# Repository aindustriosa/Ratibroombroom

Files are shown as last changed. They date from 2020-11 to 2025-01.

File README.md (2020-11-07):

# Ratibroombroom

This repository contains de design files for the electronics part of Ratibroombroom, a maze solving robot designed at [A industriosa](https://aindustriosa.org/).

The board includes an STM32F405RGT6 microcontroller and two DRV8835 H-bridge drivers moving two 610 coreless motors for locomotion. The robot will also include a suction fan mounted on top with another 610 coreless motor driven directly with an IRLML6344 mosfet.

In the sensing aspect, the robot includes four SFH4045N IR LEDs paired with four PT12-21B/TR8 IR photodiodes for wall detection and positioning inside the maze. AS5145B magnetic encoders are used to measure motor movement precisely. The robot includes an MPU9250 9 axis IMU.

For HMI, we included two tactile switches, four LEDs and a buzzer. We are also working in an external OLED display that could be mounted in a separate module.

>THIS IS A WORK IN PROGRESS AND WILL BE UPDATED AS WE ADVANCE IN THE DEVELOPMENT

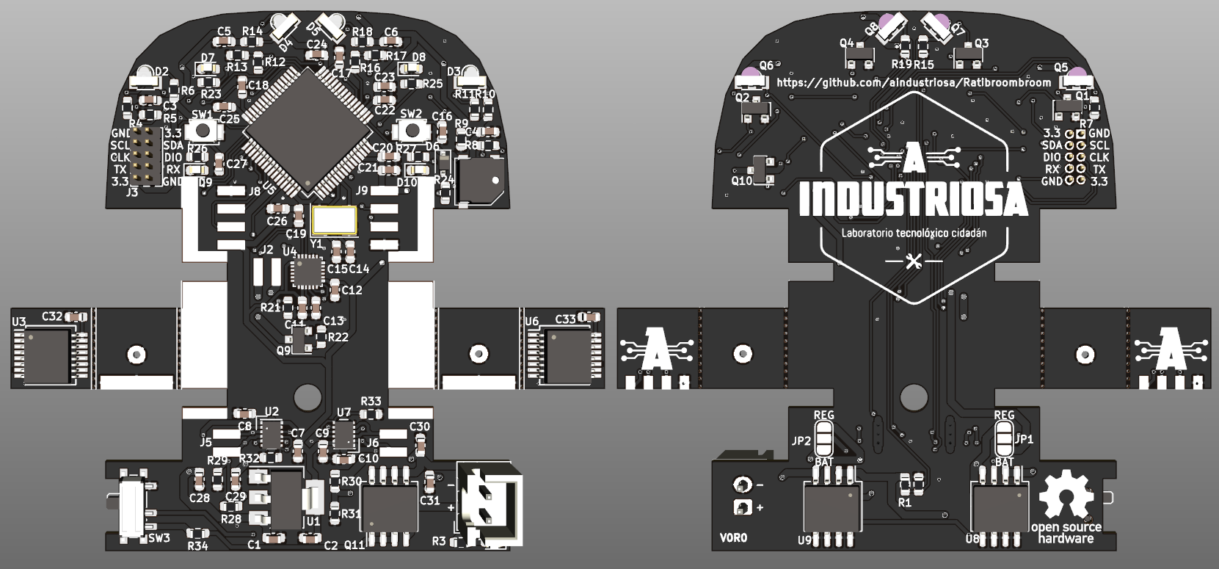
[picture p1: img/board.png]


## Software

The software for this robot will be available in the following repository: [https://github.com/aindustriosa/RatibroombroomSW/](https://github.com/aindustriosa/RatibroombroomSW/)

## Pinout 

Pin # | Function | Peripheral |
----|----|----|
2 | PC13 | Right button (SW2) | 
8 | PC0 | Receiver front right (Q6)  | 
9 | PC1 | Receiver side right (Q8) | 
10 | PC2 | Receiver side left (Q7) | 
11 | PC3 | Receiver front left (Q5) | 
14 | PA0 | LED front left (D7) | 
15 | PA1 | LED front right (D8) | 
16 | PA2 | LED back left (D9)  | 
17 | PA3 | LED back right (D10) | 
20 | PA4 | Emitter front right (D3) | 
21 | PA5 | Emitter side right (D5) | 
22 | PA6 | Emitter side left (D4) | 
23 | PA7 | Emitter front left (D2) | 
24 | PC4 | Battery voltage measurement | 
29 | PB10 | I2C SCL (J3) | 
30 | PB11 | I2C SDA (J3) | 
33 | PB12 | Left button (SW1) |  
35 | PB14 | IMU FSYNC (U4) | 
36 | PB15 | IMU INT (U4) | 
37 | PC6 | Right motor direction (U7) | 
38 | PC7 | Right motor PWM (U7) | 
39 | PC8 | Left motor direction (U2) | 
40 | PC9 | Left motor PWM (U2) | 
42 | PA9 | Serial RX (J3) | 
43 | PA10 | Serial TX (J3) | 
46 | PA13 | SWDIO (J3) | 
49 | PA14 | SWCLK (J3) | 
50 | PA15 | IMU CS (U4) | 
51 | PC10 | IMU SCK (U4) | 
52 | PC11 | IMU MISO (U4) | 
53 | PC12 | IMU MOSI (U4) | 
56 | PB4 | Encoder left, channel A | 
57 | PB5 | Encoder left, channel B | 
58 | PB6 | Encoder right, channel B | 
59 | PB7 | Encoder right, channel A | 
61 | PB8 | Suction fan PWM | 
62 | PB9 | Buzzer (BZ1) | 

## References

This project is heavily based on the work of [cua-cua](https://github.com/cua-cua) and [peque](https://github.com/peque) from [Bulebots](https://github.com/Bulebots) in their projects [Bulebule](https://github.com/Bulebots/bulebule) and [Meiga](https://github.com/Bulebots/meiga)

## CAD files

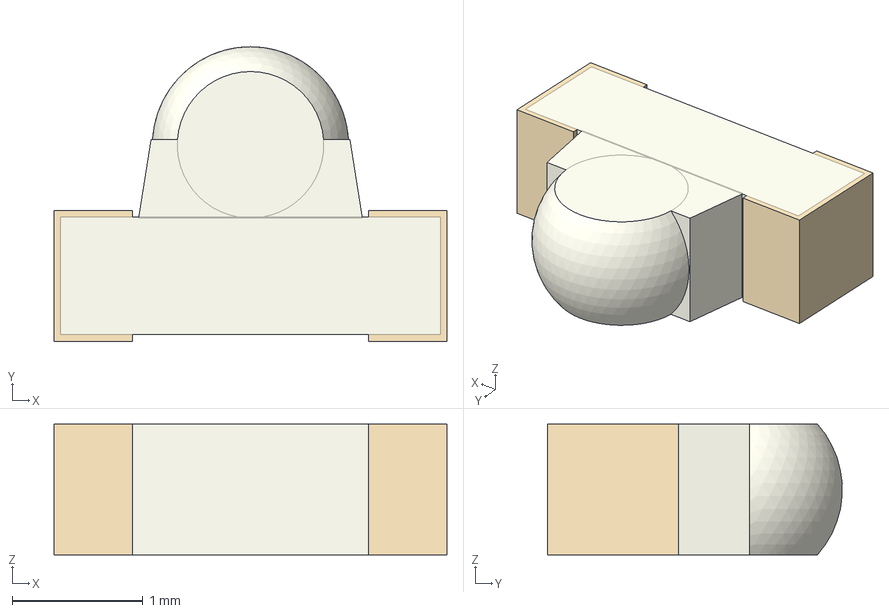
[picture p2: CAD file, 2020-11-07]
3d_models/SFH4045N.step
3.00 x 2.25 x 1.00 mm

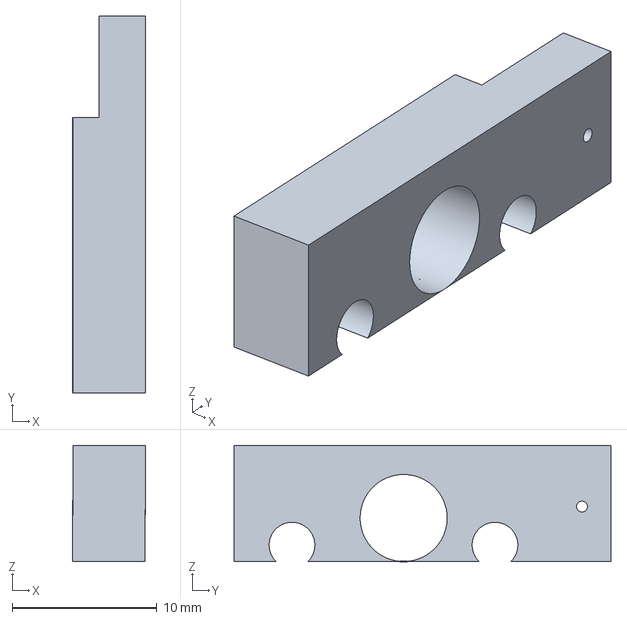
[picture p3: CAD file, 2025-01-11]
cad_design/Ratibroombroom_3d_design_motor_holder-motor_holder_cnc_tolerances.3mf
5.00 x 26.0 x 8.00 mm

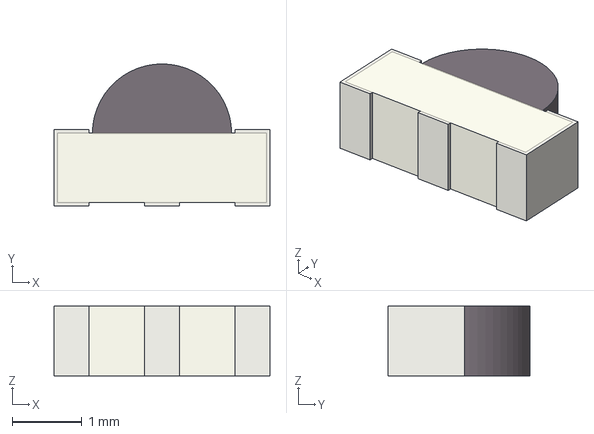
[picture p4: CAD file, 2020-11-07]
3d_models/PT12-21BTR8.step
3.10 x 2.04 x 1.00 mm

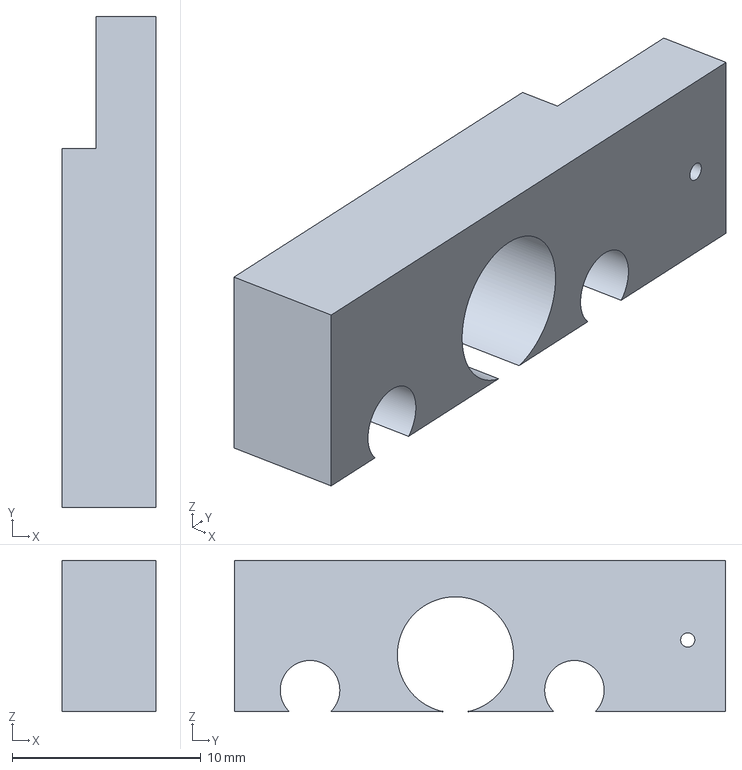
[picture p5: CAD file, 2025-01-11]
cad_design/Ratibroombroom_3d_design_motor_holder-motor_holder_3d_tolerances.3mf
5.00 x 26.0 x 8.00 mm

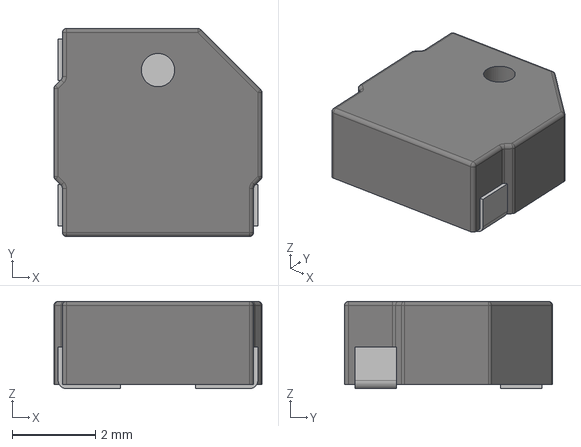
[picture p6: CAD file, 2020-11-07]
3d_models/MLT_5020.step
5.00 x 5.00 x 2.10 mm

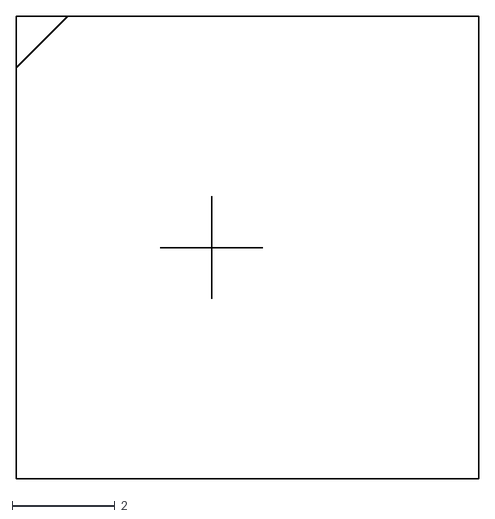
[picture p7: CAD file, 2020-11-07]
cad_design/Encoder_support_Eco1.User.dxf
9.00 x 9.00

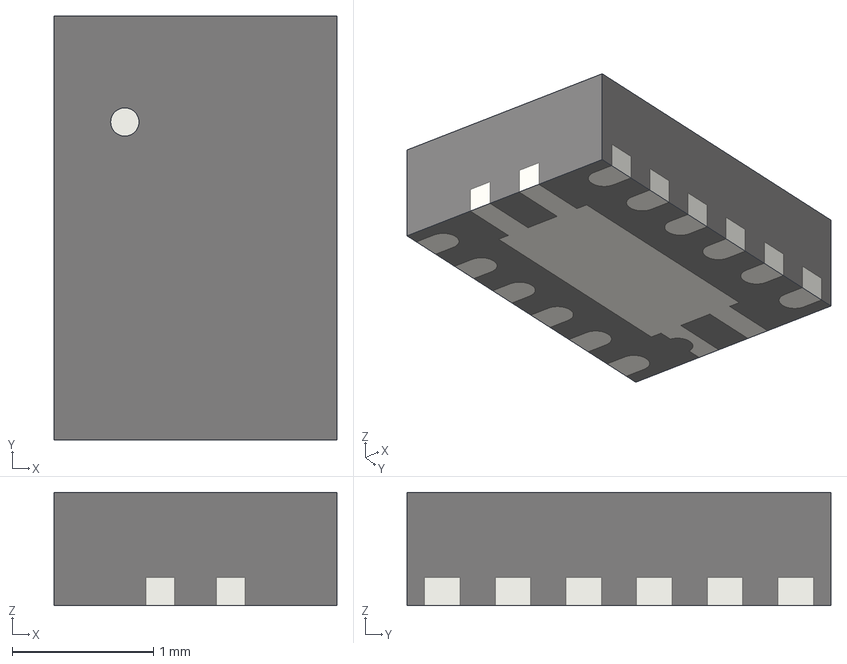
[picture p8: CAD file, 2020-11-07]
3d_models/WSON_12_1EP_3x2mm_P0_5mm_EP1x2_65.step
2.00 x 3.00 x 0.8 mm

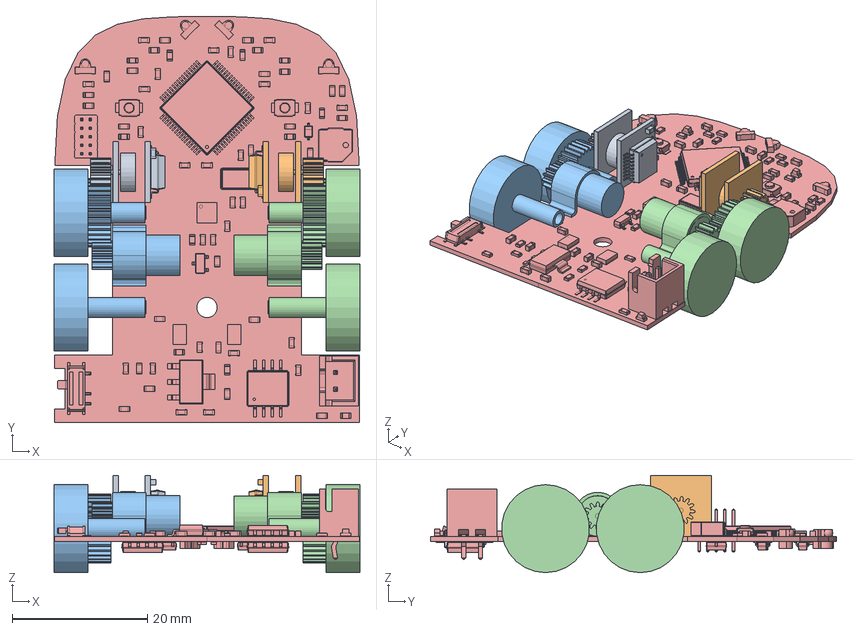
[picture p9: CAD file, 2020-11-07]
cad_design/Ratibroombroom_3d_design.FCStd
45.2 x 60.0 x 14.4 mm
Left encoder
Right encoder
Left drive
Right drive
Board

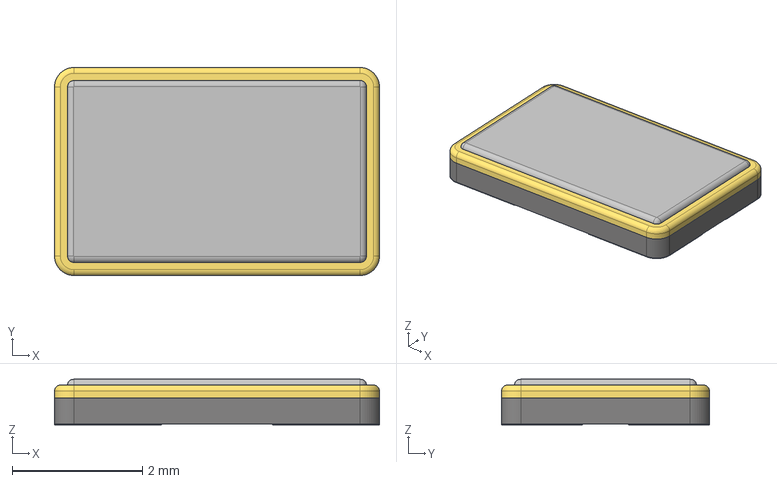
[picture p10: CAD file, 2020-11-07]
3d_models/Crystal_Crystal_SMD_5032_4Pin_5_0x3_2mm.step
5.00 x 3.20 x 0.7 mm

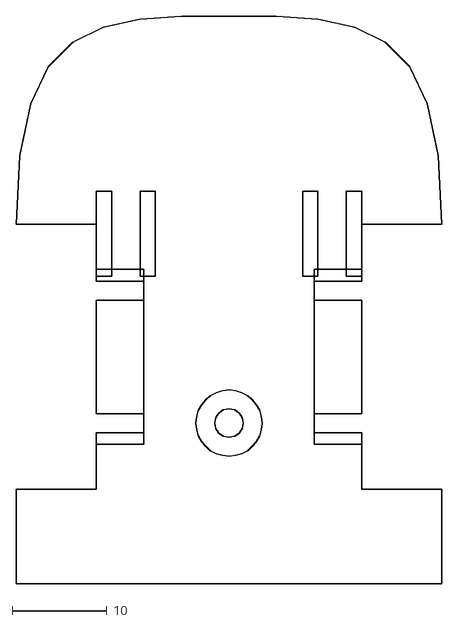
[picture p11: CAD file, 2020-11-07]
cad_design/Board_Eco1.User.dxf
45.0 x 60.0

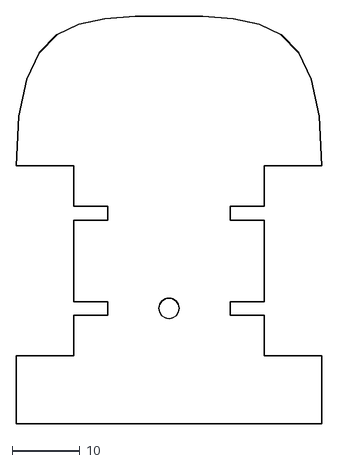
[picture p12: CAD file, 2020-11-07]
cad_design/Board_Edge.Cuts.dxf
45.0 x 60.0

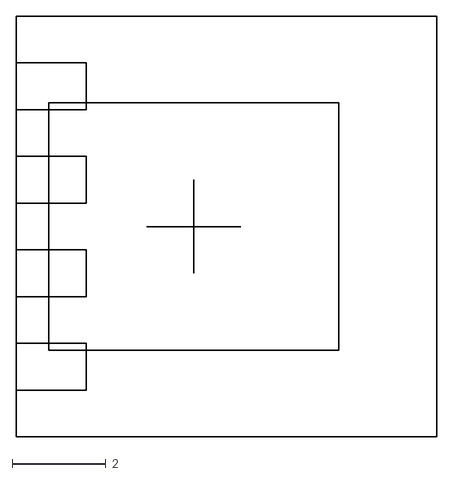
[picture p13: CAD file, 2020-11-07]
cad_design/Encoder_Eco1.User.dxf
9.00 x 9.00

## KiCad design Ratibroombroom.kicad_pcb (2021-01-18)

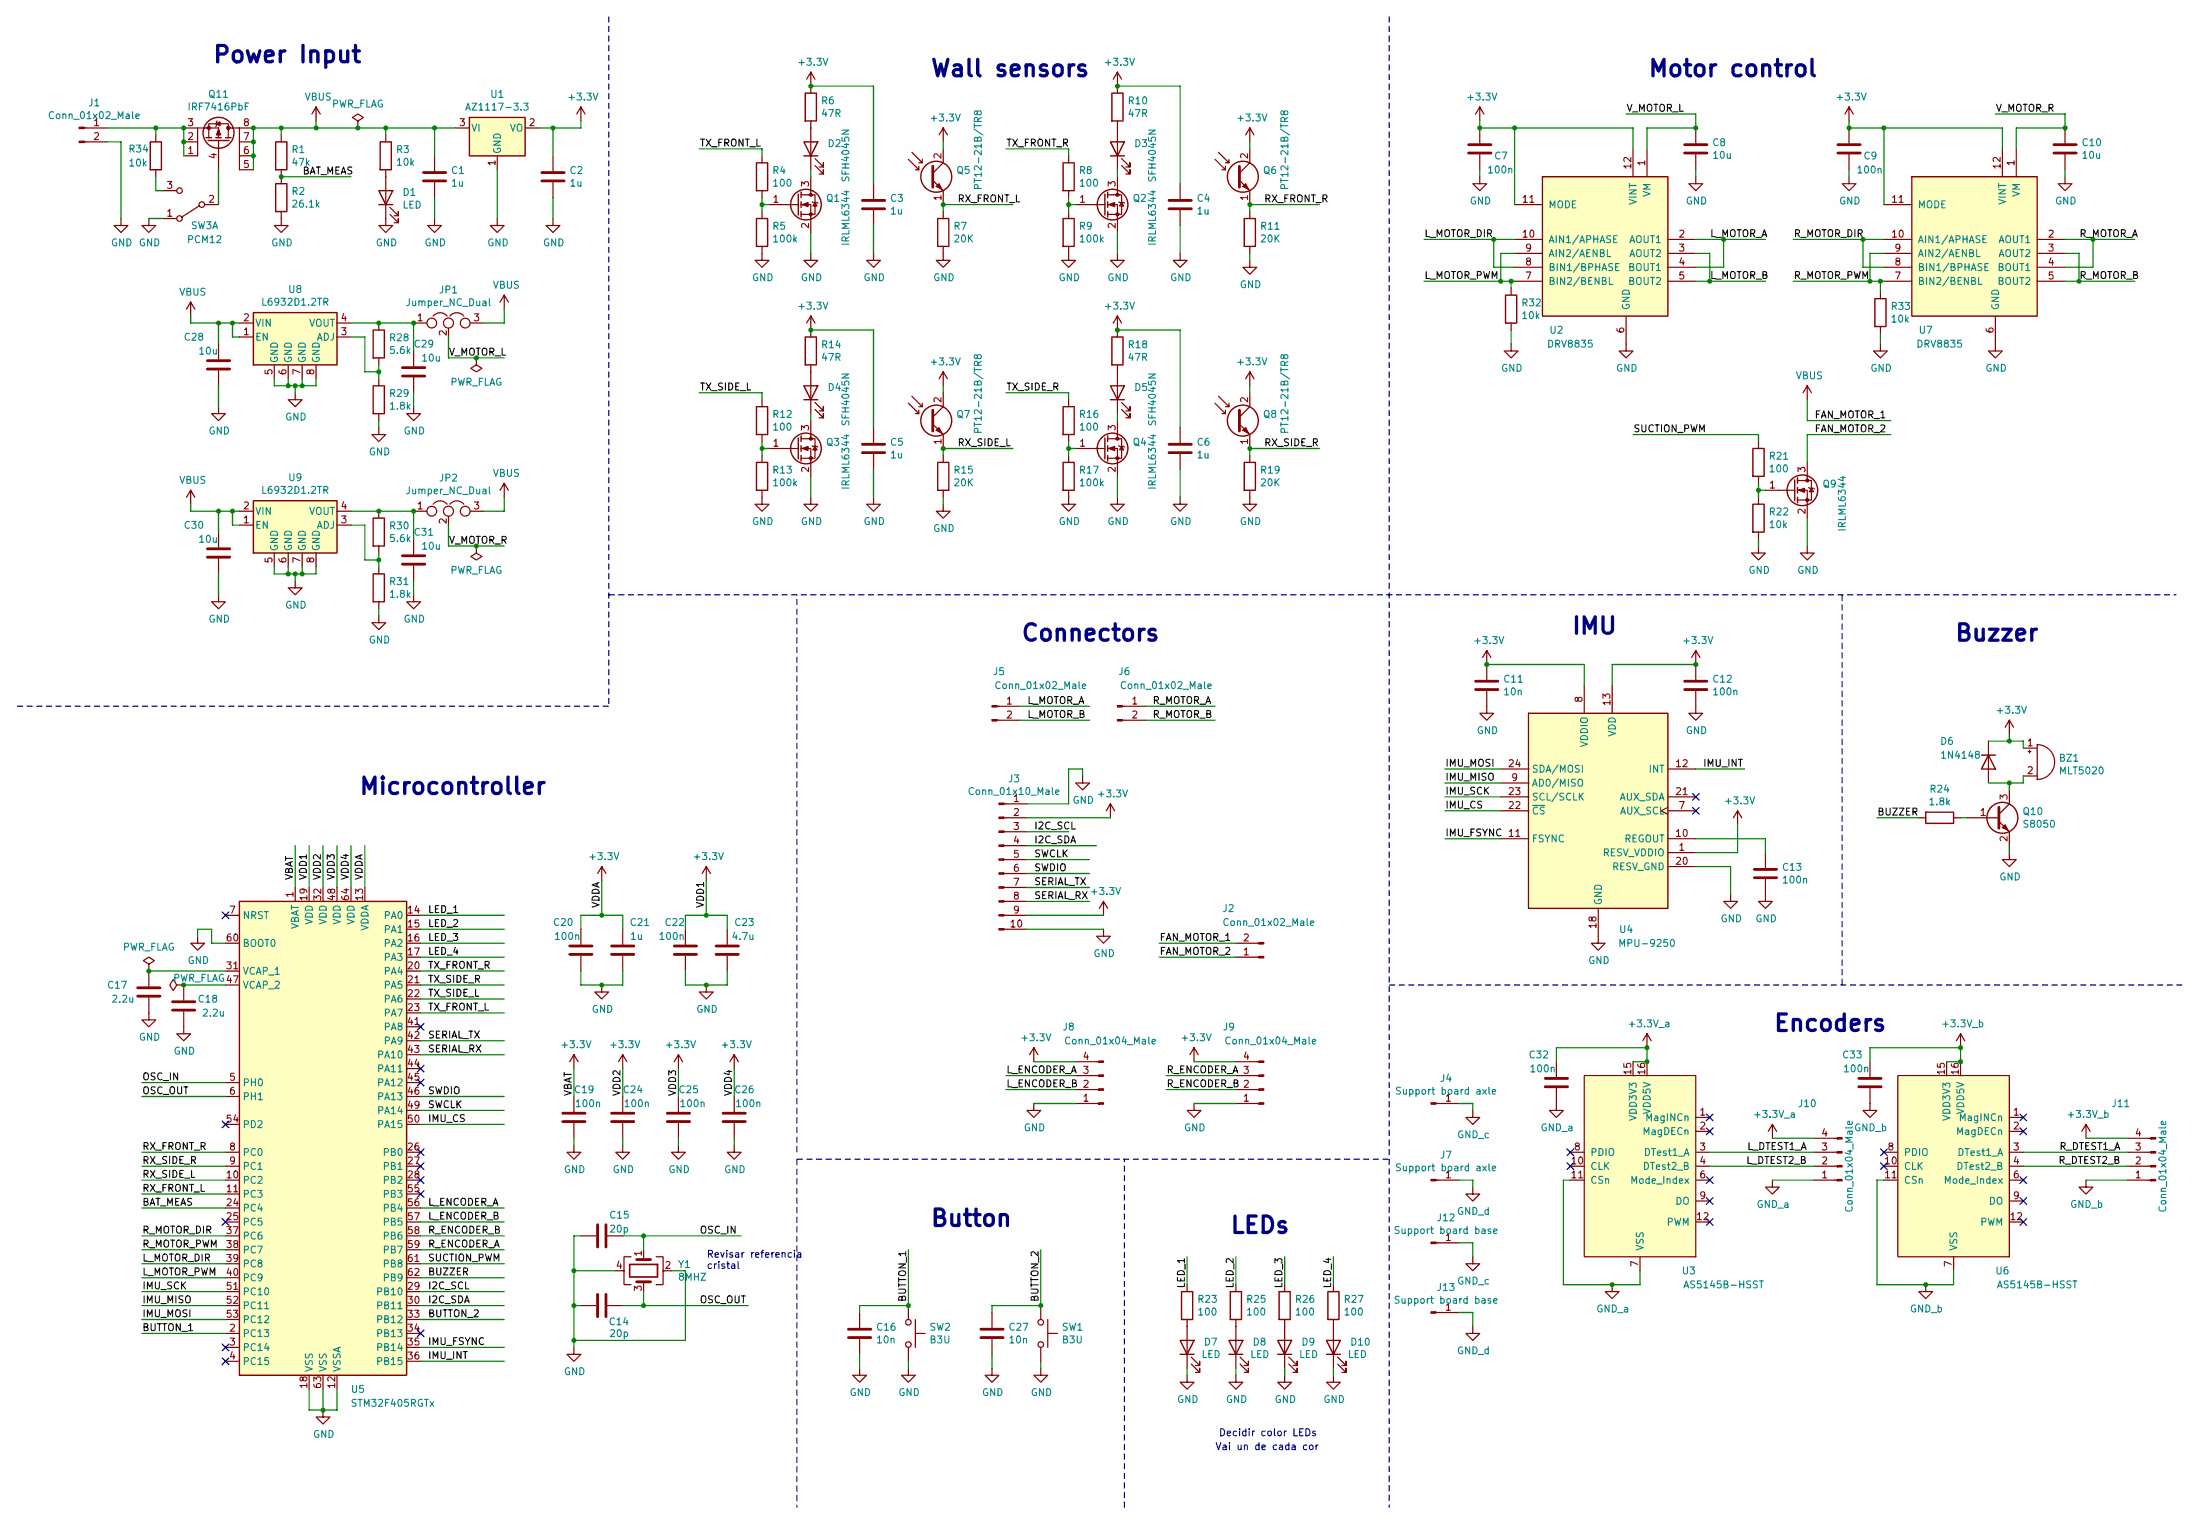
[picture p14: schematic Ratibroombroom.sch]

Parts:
BZ1: MLT5020; MLT-5020
C1, C2, C3, C4, C5, C6, C21: 1u; C_0603_1608Metric
C7, C9, C12, C13, C19, C20, C22, C24, C25, C26, C32, C33: 100n; C_0603_1608Metric
C8, C10, C28, C29, C30, C31: 10u; C_0603_1608Metric
C11, C16, C27: 10n; C_0603_1608Metric
C14, C15: 20p; C_0603_1608Metric
C17, C18: 2.2u; C_0603_1608Metric
C23: 4.7u; C_0603_1608Metric
D1, D7, D8, D9, D10: LED; LED_0603_1608Metric
D2, D3, D4, D5: SFH4045N
D6: 1N4148; D_SOD-323
J1: Conn_01x02_Male; JST_XH_B2B-XH-A_1x02_P2.50mm_Vertical
J2, J5, J6: Conn_01x02_Male; Pad_SMD_2P_1x3mm
J3: Conn_01x10_Male; PinHeader_2x05_P1.27mm_Vertical
J4, J7: Support board axle; Encoder_axle_hole
J8, J9: Conn_01x04_Male; Pad_SMD_4P_1x3mm
J10, J11: Conn_01x04_Male; Pad_SMD_4P_1x1.5mm
J12, J13: Support board base; Encoder_base_connector
JP1, JP2: Jumper_NC_Dual; SolderJumper-3_P1.3mm_Open_RoundedPad1.0x1.5mm_NumberLabels
Q1, Q2, Q3, Q4, Q9: IRLML6344; SOT-23
Q5, Q6, Q7, Q8: PT12-21B/TR8; PT12-21B-TR8
Q10: S8050; SOT-23
Q11: IRF7416PbF; SO-8_5.3x6.2mm_P1.27mm
R1: 47k; R_0603_1608Metric
R2: 26.1k; R_0603_1608Metric
R3, R22, R32, R33, R34: 10k; R_0603_1608Metric
R4, R8, R12, R16, R21, R23, R25, R26, R27: 100; R_0603_1608Metric
R5, R9, R13, R17: 100k; R_0603_1608Metric
R6, R10, R14, R18: 47R; R_0603_1608Metric
R7, R11, R15, R19: 20K; R_0603_1608Metric
R24, R29, R31: 1.8k; R_0603_1608Metric
R28, R30: 5.6k; R_0603_1608Metric
SW1, SW2: B3U; SW_SPST_B3U-1000P
SW3: PCM12; SW_SPDT_PCM12
U1: AZ1117-3.3; SOT-223-3_TabPin2
U2, U7: DRV8835; WSON-12-1EP_3x2mm_P0.5mm_EP1x2.65_ThermalVias
U3, U6: AS5145B-HSST; SSOP-16_5.3x6.2mm_P0.65mm
U4: MPU-9250; QFN-24-1EP_3x3mm_P0.4mm_EP1.75x1.6mm
U5: STM32F405RGTx; LQFP-64_10x10mm_P0.5mm
U8, U9: L6932D1.2TR; SO-8_5.3x6.2mm_P1.27mm
Y1: 8MHZ; Crystal_SMD_5032-4Pin_5.0x3.2mm

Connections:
+3.3V_a: C32.2, J10.4, U3.15 (VDD3V3), U3.16 (VDD5V)
+3.3V_b: C33.2, J11.4, U6.15 (VDD3V3), U6.16 (VDD5V)
+3V3: BZ1.1 (-), C2.1, C3.1, C4.1, C5.1, C6.1, C7.1, C9.1, C11.1, C12.1, C19.2, C20.2, C21.2, C22.2, C23.2, C24.2, C25.2, C26.2, D6.1 (K), J3.2, J3.9, J8.4, J9.4, Q5.2 (C), Q6.2 (C), Q7.2 (C), Q8.2 (C), R6.1, R10.1, R14.1, R18.1, U1.2 (VO), U2.11 (MODE), U2.12 (VINT), U4.1 (RESV_VDDIO), U4.8 (VDDIO), U4.13 (VDD), U5.1 (VBAT), U5.13 (VDDA), U5.19 (VDD), U5.32 (VDD), U5.48 (VDD), U5.64 (VDD), U7.11 (MODE), U7.12 (VINT)
/BAT_MEAS: R1.2, R2.1, U5.24 (PC4)
/BUTTON_1: C16.1, SW2.1, U5.2 (PC13)
/BUTTON_2: C27.1, SW1.1, U5.33 (PB12)
/BUZZER: R24.2, U5.62 (PB9)
/FAN_MOTOR_2: J2.1, Q9.3 (D)
/I2C_SCL: J3.3, U5.29 (PB10)
/I2C_SDA: J3.4, U5.30 (PB11)
/IMU_CS: U4.22 (~CS), U5.50 (PA15)
/IMU_FSYNC: U4.11 (FSYNC), U5.35 (PB14)
/IMU_INT: U4.12 (INT), U5.36 (PB15)
/IMU_MISO: U4.9 (AD0/MISO), U5.52 (PC11)
/IMU_MOSI: U4.24 (SDA/MOSI), U5.53 (PC12)
/IMU_SCK: U4.23 (SCL/SCLK), U5.51 (PC10)
/LED_1: R23.1, U5.14 (PA0)
/LED_2: R25.1, U5.15 (PA1)
/LED_3: R26.1, U5.16 (PA2)
/LED_4: R27.1, U5.17 (PA3)
/L_DTEST1_A: J10.3, U3.3 (DTest1_A)
/L_DTEST2_B: J10.2, U3.4 (DTest2_B)
/L_ENCODER_A: J8.3, U5.56 (PB4)
/L_ENCODER_B: J8.2, U5.57 (PB5)
/L_MOTOR_A: J5.1, U2.2 (AOUT1), U2.4 (BOUT1)
/L_MOTOR_B: J5.2, U2.3 (AOUT2), U2.5 (BOUT2)
/L_MOTOR_DIR: U2.8 (BIN1/BPHASE), U2.10 (AIN1/APHASE), U5.39 (PC8)
/L_MOTOR_PWM: R32.1, U2.7 (BIN2/BENBL), U2.9 (AIN2/AENBL), U5.40 (PC9)
/OSC_IN: C15.1, U5.5 (PH0), Y1.1
/OSC_OUT: C14.1, U5.6 (PH1), Y1.3
/RX_FRONT_L: Q5.1 (E), R7.1, U5.11 (PC3)
/RX_FRONT_R: Q6.1 (E), R11.1, U5.8 (PC0)
/RX_SIDE_L: Q7.1 (E), R15.1, U5.10 (PC2)
/RX_SIDE_R: Q8.1 (E), R19.1, U5.9 (PC1)
/R_DTEST1_A: J11.3, U6.3 (DTest1_A)
/R_DTEST2_B: J11.2, U6.4 (DTest2_B)
/R_ENCODER_A: J9.3, U5.59 (PB7)
/R_ENCODER_B: J9.2, U5.58 (PB6)
/R_MOTOR_A: J6.1, U7.2 (AOUT1), U7.4 (BOUT1)
/R_MOTOR_B: J6.2, U7.3 (AOUT2), U7.5 (BOUT2)
/R_MOTOR_DIR: U5.37 (PC6), U7.8 (BIN1/BPHASE), U7.10 (AIN1/APHASE)
/R_MOTOR_PWM: R33.1, U5.38 (PC7), U7.7 (BIN2/BENBL), U7.9 (AIN2/AENBL)
/SERIAL_RX: J3.8, U5.43 (PA10)
/SERIAL_TX: J3.7, U5.42 (PA9)
/SUCTION_PWM: R21.1, U5.61 (PB8)
/SWCLK: J3.5, U5.49 (PA14)
/SWDIO: J3.6, U5.46 (PA13)
/TX_FRONT_L: R4.1, U5.23 (PA7)
/TX_FRONT_R: R8.1, U5.20 (PA4)
/TX_SIDE_L: R12.1, U5.22 (PA6)
/TX_SIDE_R: R16.1, U5.21 (PA5)
/V_MOTOR_L: C8.1, JP1.2, U2.1 (VM)
/V_MOTOR_R: C10.1, JP2.2, U7.1 (VM)
GND: C1.2, C2.2, C3.2, C4.2, C5.2, C6.2, C7.2, C8.2, C9.2, C10.2, C11.2, C12.2, C13.2, C14.2, C15.2, C16.2, C17.1, C18.1, C19.1, C20.1, C21.1, C22.1, C23.1, C24.1, C25.1, C26.1, C27.2, C28.1, C29.1, C30.1, C31.1, D1.1 (K), D7.1 (K), D8.1 (K), D9.1 (K), D10.1 (K), J1.2, J3.1, J3.10, J8.1, J9.1, Q1.2 (S), Q2.2 (S), Q3.2 (S), Q4.2 (S), Q9.2 (S), Q10.2 (E), R2.2, R5.2, R7.2, R9.2, R11.2, R13.2, R15.2, R17.2, R19.2, R22.2, R29.2, R31.2, R32.2, R33.2, SW1.2, SW2.2, SW3.1 (A), U1.1 (GND), U2.6 (GND), U4.18 (GND), U4.20 (RESV_GND), U5.12 (VSSA), U5.18 (VSS), U5.60 (BOOT0), U5.63 (VSS), U7.6 (GND), U8.5 (GND), U8.6 (GND), U8.7 (GND), U8.8 (GND), U9.5 (GND), U9.6 (GND), U9.7 (GND), U9.8 (GND), Y1.2, Y1.4
GND_a: C32.1, J10.1, U3.7 (VSS), U3.11 (CSn)
GND_b: C33.1, J11.1, U6.7 (VSS), U6.11 (CSn)
GND_c: J4.1, J12.1
GND_d: J7.1, J13.1
unnamed: BZ1.2 (+), D6.2 (A), Q10.3 (C)
unnamed: C13.1, U4.10 (REGOUT)
unnamed: C17.2, U5.31 (VCAP_1)
unnamed: C18.2, U5.47 (VCAP_2)
unnamed: C29.2, JP1.1, R28.1, U8.4 (VOUT)
unnamed: C31.2, JP2.1, R30.1, U9.4 (VOUT)
unnamed: D1.2 (A), R3.2
unnamed: D2.1 (K), Q1.3 (D)
unnamed: D2.2 (A), R6.2
unnamed: D3.1 (K), Q2.3 (D)
unnamed: D3.2 (A), R10.2
unnamed: D4.1 (K), Q3.3 (D)
unnamed: D4.2 (A), R14.2
unnamed: D5.1 (K), Q4.3 (D)
unnamed: D5.2 (A), R18.2
unnamed: D7.2 (A), R23.2
unnamed: D8.2 (A), R25.2
unnamed: D9.2 (A), R26.2
unnamed: D10.2 (A), R27.2
unnamed: J1.1, Q11.1 (S), Q11.2 (S), Q11.3 (S), R34.1
unnamed: Q1.1 (G), R4.2, R5.1
unnamed: Q2.1 (G), R8.2, R9.1
unnamed: Q3.1 (G), R12.2, R13.1
unnamed: Q4.1 (G), R16.2, R17.1
unnamed: Q9.1 (G), R21.2, R22.1
unnamed: Q10.1 (B), R24.1
unnamed: Q11.4 (G), SW3.2 (B)
unnamed: R28.2, R29.1, U8.3 (ADJ)
unnamed: R30.2, R31.1, U9.3 (ADJ)
unnamed: R34.2, SW3.3 (C)
VBUS: C1.1, C28.2, C30.2, J2.2, JP1.3, JP2.3, Q11.5 (D), Q11.6 (D), Q11.7 (D), Q11.8 (D), R1.1, R3.1, U1.3 (VI), U8.1 (EN), U8.2 (VIN), U9.1 (EN), U9.2 (VIN)

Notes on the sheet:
Power Input
Wall sensors
Motor control
Button
LEDs
IMU
Buzzer
Encoders
Microcontroller
Connectors
Decidir color LEDs
Revisar referencia cristal
Vai un de cada cor

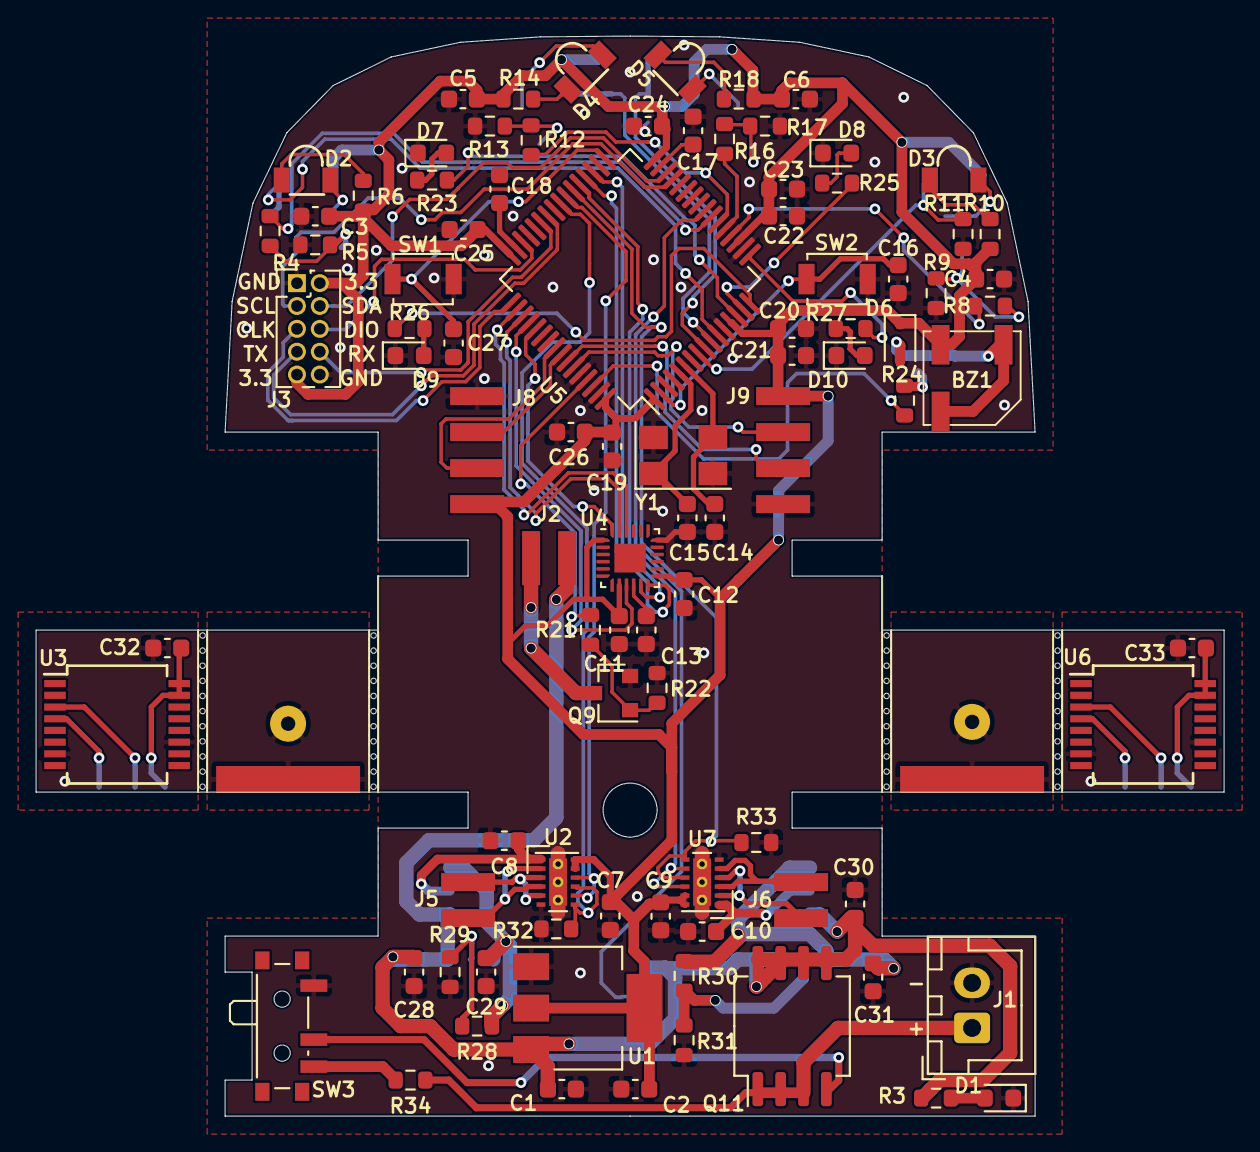
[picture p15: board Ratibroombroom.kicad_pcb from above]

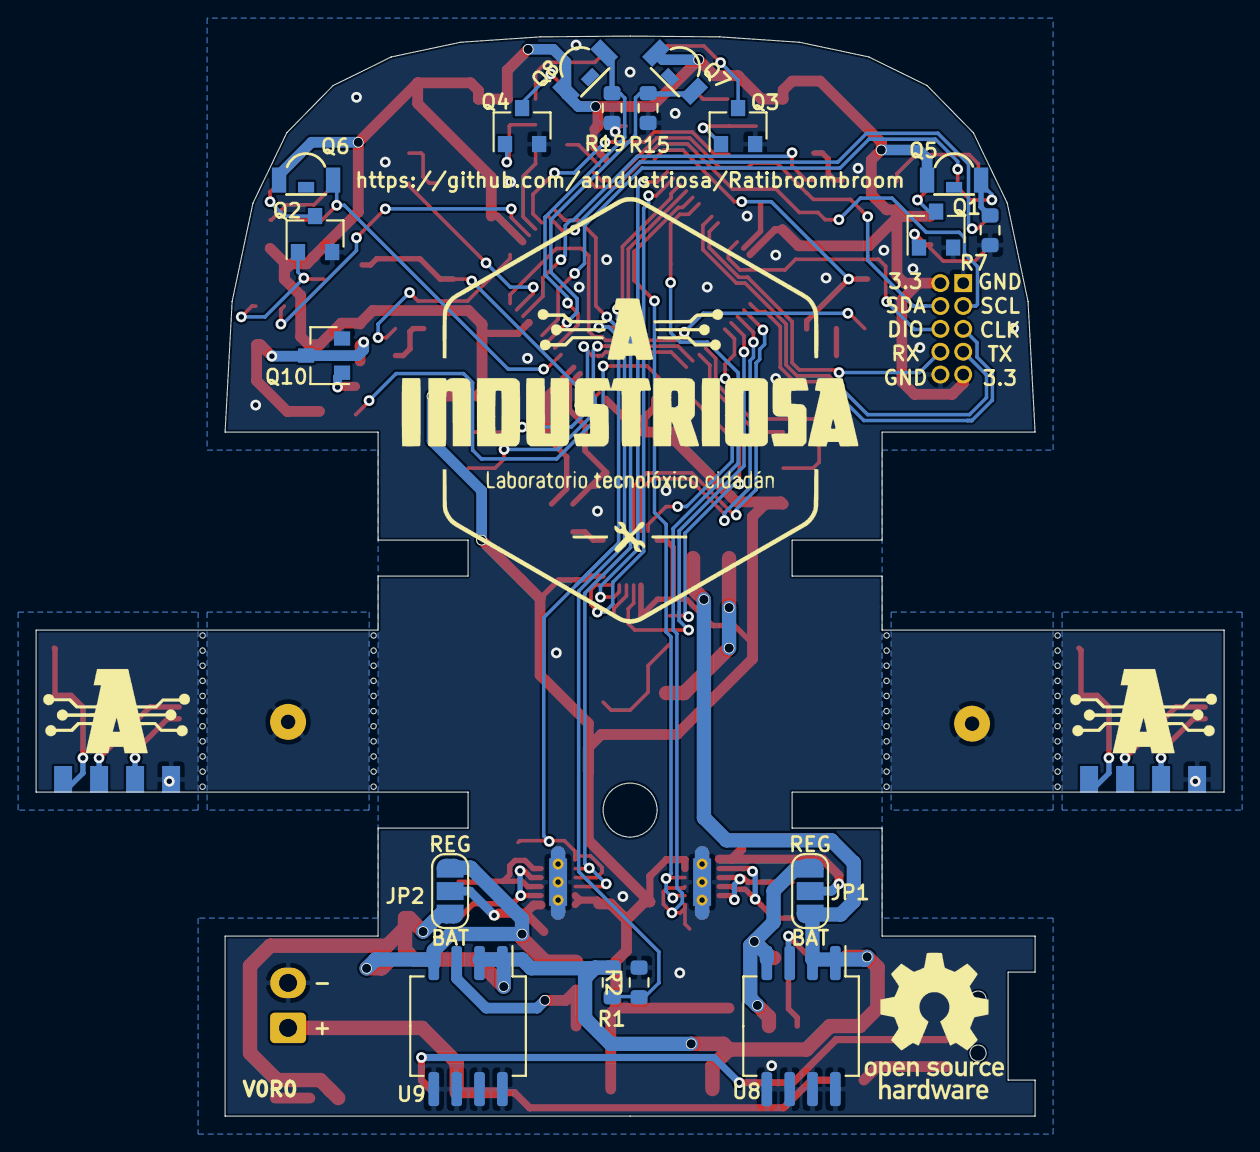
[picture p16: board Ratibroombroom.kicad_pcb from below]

Board: 2 copper layers, 66.0 x 60.0 mm, 116 parts (20 on the bottom side), 89 nets.

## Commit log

2020-01-16 First version of the micromouse schematic
    [Ratibroombroom.kicad_pcb, Ratibroombroom.sch]
2020-01-17 Add linear regulators to motor drivers supply. Include jumpers to select between direct (battery), regulated or none supply for the drivers.
    [Ratibroombroom.sch]
2020-01-17 Added pull-down resistors on motor pwm lines
    [Ratibroombroom.sch]
2020-01-17 Added comments in schematics
    [Ratibroombroom.sch]
2020-01-17 More comments on schematics
    [Ratibroombroom.sch]
2020-01-17 Typo fix
    [Ratibroombroom.sch]
2020-01-18 Modify connection of capacitors in IR emitters. Add on/of switch through mosfet. Assign footprints to every schematic symbol.
    [Ratibroombroom.sch]
2020-01-18 Added BOM parts for Power section
    [Ratibroombroom.sch]
2020-01-19 Added BOM parts for Motor control section
    [Ratibroombroom.sch]
2020-01-19 Added BOM parts for IMU section
    [Ratibroombroom.sch]
2020-01-19 Added BOM parts for Buzzer section
    [Ratibroombroom.sch]
2020-01-19 Added BOM parts for Button and LED sections
    [Ratibroombroom.sch]
2020-01-19 Added BOM parts for Microcontroller section
    [Ratibroombroom.sch]
2020-01-19 Added BOM parts for Encoder section
    [Ratibroombroom.sch]
2020-01-19 Added BOM parts for Wall Sensor section
    [Ratibroombroom.sch]
2020-01-19 Fix wrong footpring for DRV8835
    [Ratibroombroom.sch]
2020-01-19 Add decoupling capacitors to the magnetic encoders
    [Ratibroombroom.sch]
2020-01-19 Fix wrong footprint for MPU-9250
    [Ratibroombroom.sch]
2020-01-19 Fix incomplete commit 51b0672
    [Ratibroombroom.sch]
2020-01-19 Redo edge connector used for encoder boards
    [Ratibroombroom.sch]
2020-01-19 Remove solder paste from motor and encoder board connector footprints
2020-02-14 Fix error assigning power supply to the right motor driver
    [Ratibroombroom.sch]
2020-02-14 Add mouse 3D design file made with Freecad
    [Ratibroombroom_3d_design.FCStd]
2020-02-14 Add generated dxf layers for pcbnew
    [Board_Eco1.User.dxf, Board_Edge.Cuts.dxf, Encoder_Eco1.User.dxf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]
2020-02-14 Test dxf graphics in pcbnew
    [Ratibroombroom.kicad_pcb]
2020-02-15 Modify board to 45mm width to make everything fit. Place components in pcbnew Modify schematic to merge I2C, SWIO and UART connectors into a single 2x5 pin connector
    [Ratibroombroom.kicad_pcb, Ratibroombroom.sch]
2020-02-15 Modify 3D design to fit the 45mm width board
    [Board_Edge.Cuts.dxf, Ratibroombroom_3d_design.FCStd]
2020-02-15 Change encoder board connector footprint to single side connector
    [Ratibroombroom.kicad_pcb, Ratibroombroom.sch]
2020-09-29 Partial PCB routing
    [Ratibroombroom.route1.kicad_pcb, Ratibroombroom.route2.kicad_pcb, Ratibroombroom.sch]
2020-10-06 More PCB routing. Add encoder magnet support boards. Include 3D models that were missing. Clean silkscreen layers. Update 3d CAD design. Include .step model of the robot.
    [Board_Eco1.User.dxf, Board_Edge.Cuts.dxf, Crystal_Crystal_SMD_5032_4Pin_5_0x3_2mm.step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]
2020-10-14 Change encoder board connectors so that the boards will be rotated in the final assembly. Add separate ground and power nets to encoder boards to pass DRC cleanly. Add some logos
    [Ratibroombroom.kicad_pcb, Ratibroombroom.sch]
2020-10-16 Add version tag in silkscreen. Change board thickness to .8 mm
    [Ratibroombroom.kicad_pcb]
2020-10-19 Add BOM references
    [Ratibroombroom.kicad_pcb, Ratibroombroom.sch]
2020-11-07 Remove discarded routing attempts
    [Ratibroombroom.route1.kicad_pcb, Ratibroombroom.route2.kicad_pcb]
2021-01-18 Change R24 value to 1k8 to increase buzzer loudness
    [Ratibroombroom.kicad_pcb, Ratibroombroom.sch]
2021-09-25 Include encoder axle supports in CAD design
2025-01-11 WIP: motor holder 3d design
    [Ratibroombroom_3d_design_motor_holder-motor_holder_3d_tolerances.3mf, Ratibroombroom_3d_design_motor_holder-motor_holder_cnc_tolerances.3mf]
